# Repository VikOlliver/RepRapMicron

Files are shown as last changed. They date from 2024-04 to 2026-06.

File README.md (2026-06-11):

# RepRapMicron (μRepRap)

## Overview

The RepRapMicron Project, or μRepRap, is an extension of the Open Source RepRap 3D printer project that aims to bring micron-scale fabrication into very widespread adoption. The main project page is [here](https://reprap.org/wiki/RepRapMicron) and currently the assembly instructions are on the Github wiki. It uses hardware and software familiar to 3D printer and CNC developers (GCODE, GRBL, NEMA17 steppers etc.), and materials that are easily and inexpensively available.

As of PIKA V0.02 pixels can be placed or engraved with repeatable micron precision in 2D without difficulty. Range of motion is approximately 8mm on X, Y, and Z axes. A resin deposition system for <4μm droplets is functional if not complete. Current resin material is "Top Coat" Nail Art UV Gel.

The meaty part is in the "pika" directory, where the OpenSCAD models for a 3D printed print-in-place flexure chassis and axis drivers can be found. Parts are intended to fit a 10mm grid and attach with M3 fasteners.

The PIKA version is now the focus of development, and departs from MAUS in that it is specifically a μRepRap design, rather than a kit of parts for constructing μRepRaps. If you want to make the best practical machine rather than a flexure research platform, PIKA is the preferred version.

The project has achieved the fourth Alpha release. This repository holds files that can reasonably be expected to be functional and useful to potential developers/experimenters.

If you're looking for pre-built STL files for MAUS, they're [here](https://www.printables.com/model/1286343-reprapmicron-micron-accurate-3d-printer). PIKA is [here](https://www.printables.com/model/1692745-reprapmicron-pika-micron-resolution-3d-printer). Note that Printables is not automatically kept in sync with the source or instructions.

## Roadmap

1. Develop a micron-accurate, 3D printable mechanism. - UNLOCKED
2. Develop a print head for it. - UNLOCKED
3. Make more of them - UNLOCKED
4. Develop practical 3D deposition for resin and other materials.
5. Reduce further to nanoscale
6. Take over the world

## Directory Structure

### gcode_segmentation
Python code to take GCODE from a 3D printer slicing program such as PrusaSlicer, and break it into GCODE for a series of points that can be invidivually deposited with the probe. There is provision for a routine to "re-ink" the probe tip after a predetermined number of points are deposited.

### library
A Selection of useful OpenSCAD libraries used in generating "Metriccano" modular components (10mm grid, metric fasteners), screw holes, motor mounts etc.

### maus
**M**icron **A**ccurate **U**niversal **S**ystem - OpenSCAD model files for micron precision axis components based on flexures.

The maus directory contains standard axis drivers, XY complementary flexure Table, Z Tower, and probe parts that need screwing down to a solid surface. It can be assembled on a Metriccano baseboard supplied for lasercutting as metriccano_baseboad.svg, or a 12 x 14 hole piece of 10mm pitch perf board.

As of V0.05 a pantograph-like driver with parallelogram flexures - maus_parallelogram_axis_driver.scad - is used as the Axis Driver. This is linear in action rather than the earlier small-arc pivoting Axis Drivers, has a greater range of motion (~8mm TBD), and due to the linear motion of the drive nut has lower friction allowing higher acceleration and motion speed.

Assembly documentation for a functional release is on the Github Wiki, with configuration and usage instructions next up. Bill Of Materials available for V0.03 .

### pika
**P**rint **I**n-place **K**inematic **A**ssembly - OpenSCAD model files for a flexure-based axis system. The XY Table mechanism is print-in-place, making it more rigid and easier to assemble. Axis Drivers are similar to MAUS but have a modifed motor bracket component.

### png_to_gcode
Python code that reads a PNG bitmap and emits GCODE that will probe a corresponding point on the GCODE-controlled hardware. Pitch, brightness level and so forth can be provided on the command line. Intended for using RepRapMicron in dip-pen mode with bitmap files, but probably has other uses.

### oldGRBLdelta
A python/Zelle Control Panel that drives a GRBL CNC using xyz steppers and uses them to control an OpenFlexure microscope delta stage.

### utils
Utilities for calibration and assembly.

## Contributing
Please do join in. We need everything. Coders, makers, nanoscience experts, materials scientists, 3D printing experts, manual writers, graphics artists, dancers, the works. Well, maybe not the dancers.

The main repository of knowledge is the wiki on the [main project page](https://reprap.org/wiki/RepRapMicron). General updates go on [the blog](http://blog.reprap.org/). There is some coverage on the Facebook RepRap page, and commentary is welcomed.

## Licence
GPL V3 or later

## Project status
### PIKA V0.02

Fourth release candidate. Now the focus of development. Build process has been documented, other documentation relies on its compatibility with MAUS.

### MAUS V0.05

Third Alpha release candidate designed for flexure research. Essentially a modification to use PIKA-style linear Axis Drivers.

### MAUS V0.04

The prefereble build if documentation is required. V0.04 documentation is currently a list of fixups for V0.03 docs.

### MAUS V0.03

First ever Alpha release. Tested build with a few known flaws and full build documentation on wiki.

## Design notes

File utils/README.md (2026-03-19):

# RepRapMicron (μRepRap) Utilities

## Overview

This directory contains a number of utilites for aligning and calibrating the μRepRap axes.

## backlash_vernier.py

Creates a GCODE file for determining backlash on either the X (default) or Y axis. Use --help for details. Intended to be used with a probe engraving a marker substrate.

The default settings draw two sets of lines, one drawn away from the origin at a spacing increasing by 0.5μm each time, the other drawn towards the origin at constant spacing.

By observing the point at which the lines appear to align, the amount of backlash can be determined. Remember that backlash is occurring in both sets of lines in opposite directions.

## grid_gcode.py

Creates GCODE to draw a grid, default settings 10 x 10 squares of 100μm. THe grid is created using full-length lines across the grid rather than by drawing each square individually.
Useful for determining overall behaviour of the axes when engraving with the probe on a marker substrate.

## levelling_probe.py

Directly drives GCODE-based CNC through a USB serial port. μRepRap is fitted with a Touch Plate - a conductive flat slide connected to one side of the Z Touch CNC input.

This console-based utility does a simple probe on an area (by default 1mm on each side) and indicates the highest corner, lowest corner, and the overall height variation.

Given the accuracy of a foil-covered slide, a height variation of under 4μm is considered reasonable.

It is advisable to run this utility serveral times before relying on any given values because the probe physically interacts with the surface and it may take a few passes for things to stabliize.

The wider the area covered, the more accurate overall levelling will be.

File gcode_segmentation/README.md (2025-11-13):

# RepRapMicron (μRepRap) "Dipify" GCODE Segmentation

## Overview

These are the files used by The RepRapMicron Project, or μRepRap, to create GCODE from an STL or SVG file using PrusaSlicer that will draw the lines with individual dots of resin. Currently only works with one layer.

It is designed to emit GCODE on a scale of 1mm to 1 micron in the PrusaSlicer config, hopefully the same as you have configured your GRBL or other CNC controller to. Because PrusaSlicer cannot cope with print widths and layer heights on this scale, a scaling factor (set to 10 by default) lets you work on a scale of 1mm to 10 microns. Note that the scaling factor applies to both distance and speed.

## How it works

When you export the sliced model, the prusa_filter.sh bash script takes Prusa's GCODE filename as the first parameter. It is basically there to handle temporary files and call some python. I found it useful for debugging so I left it there.

The dipify_gcode.py looks for the first "Layer" comment in the GCODE and uses that to determine the layer height. It then scans the GCODE to find lines drawn below the safe Z height and breaks those line into segments. The probe is lowered to the current layer height to touch the print bed and leave a resin dot. These segments are smaller than the resin dot RepRapMicron deposits, so a line of joined dots will be created.

Some GCODE such as A axis movement and M commands are discarded.

After a given number of dots are deposited, the probe is taken to the reservoir coordinates and dipped in resin. A UV LED on the coolant output of the CNC controller is briefly turned on while the probe is in the resin reservoir (note: this is protected from the UV). Then it returns to the last point and continues.

The points are sanity checked for proximity, so for things like arcs constructed of many short lines, points are not deposited on top of one another.

At the start of each layer other than the first, the probe is dunked in the resin and the UV LED is turned on to solidify the layer.

At the end of the GCODE the script expects to find a "; *END" comment, at which point it will safely move the probe into the reservoir and do a final and longer UV exposure.

## Notable WeirdnessCompared To Conventional Extruders

FFF extruders squirt plastic down from a known height. The RepRapMicron deposits resin at the layer height, with the resin buildup above the probe tip. To work around the slicer implications, print the first layer with a negligible layer height.

FFF Extruders will drop their exudate down towards the bed, and if the layer height is set a bit tall a loosely consolidated print will result. If the RepRapMicron probe does not reach a previous layer when attempting a second layer it will not deposit any resin there or on subsequent layers and you get no output at all.

## Setting up

Load a new slide into the RepRapMicron, add a thin smear (not a drop) of resin on the foil contact plate right up to the folded over edge of the plate. Do not get resin on the folded part. That is the barrier between the resin and the build area.

Position the probe over the glass slide nearby.

Using your CNC control software move over the resin and do a "Z Touch" with the probe.

Raise the probe 100 microns or so and move it to an area of glass where you will not be depositing resin. Lower the probe to about 5 microns over the glass, or until it just deposits a droplet of resin in the slide (you'll have to move the probe up and sideways to spot it).

Set this as the Z zero and raise the probe to 100 microns or so again. Move the probe above the resin, lower it until it is in the resin. This is your reservor Z value, typically around 25μm and once determined seldom needs adjustment. Reservoir X and Y are variables in the script, but it is very convenient to arrange things so that the reservoir is at X=0, Y=-1000.

Do not get the probe too close to the reservoir edge or the UV light will solidify resin on the probe.

Load the GCODE into your CNC control software and run, finger poised over the HALT switch in a distrustful manner.

Fine tuning segment sizes and number of points per dip is left as an exercise to the diligent student.

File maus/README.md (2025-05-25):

# **M**icron **A**ccurate **U**niversal **S**ystem- “Maus”

## Overview
Maus is a collection of micron-accurate components based on 3D printed flexures. These can be combined into a multi-axis motion stage allowing a probe (or probes) to be manipulated.

The probe can be manoeuvred around a standard 25mm x 75mm glass microscope slide. Micron-level movement in the default configuration is expected to be possible inside a 4mm cube, and non-destructive movement (basically to get the probe out of the way) inside an 8mm cube. The probe can be used as a dip pen for depositing UV resin and other liquids from a reservoir on the slide. The probe is conductive and can be used to scan conductive objects via a ground wire on the slide holder.

A window in the stage allows UV exposure of the resin from underneath without illuminating the reservoir. Motion is achieved with a 400 step NEMA17 stepper motor on each axis driver, and these are controlled by any method convenient for the user.

The intention is that the probe will also be used to manipulate or even operate micron-scale items.

## Build
The *maus* directory contains three main Maus OpenSCAD build files, a design for a probe box, and the deprecated XY Table design:

**maus_axis_driver.scad** has the flexure-based precision axis driver design that is driven by a NEMA17 stepper motor.

**maus_complementary.scad** is the XY Table and stage design using complementary flexures. These have the great advantage that they do not move much in the Z axis when moving in the X & Y axes. Also contains clamp design for cylindrical USB miscroscopes.

**flexure_linear_coupling.scad** is a model for a couping that press fits on a NEMA17 motor shaft, and given sufficient downward pressure can hold a modified M3x50 screw. The screw has the head filed down in a drill so that it is narrower in diameter than the narrowest axis of an M3 nut, and the nut is screwed all the way down to the head, where it is secured with Loktite. The tapered hexagonal hole in the top of the coupling holds on to the nut.

**probe_electrolysis_grip.scad** provides a convenient jig for making micron probe tips from 28ga stainless steel or nichrome wire. 5% salt solution is used as the electrolyte, and the extremely simple process is described at [https://www.printables.com/model/874566](https://www.printables.com/model/874566).

## Deprecated

**maus_stage_deprecated.scad** Original XY Table design, now deprecated. Has at its bottom three *if (true/false)* statements used to print a selected set of parts for either an axis driver (you probably want three of those), a slide probe assembly, or an XY Table. It uses SCAD files included from the ../include directory.

**metriccano_flexures.scad** Deprecated. Has the 2-way flexure joints used for an XY Table in it, and is included by maus_stage_deprecated.scad . This should probably be in the include directory, but there are too many dependencies, I haven't figured out a nice way yet, and deprecated anyway.

## Recommended Software
To control the stepper motors, an Arduino running GRBL and a 3-axis GRBL stepper shield are adequate. GCODE can be conveniently output by 3D printer or CNC programs, though it is recommended that a scale of 1mm to 1 micron is used to avoid floating point errors. The author uses an Arduino Mega running GRBL and driving a RAMPS1.4 3D printer control board. To generate the GCODE they use Inkscape to create SVG files, convert those to GCODE with jscut, and use cncjs as a control console. There are also a number of Python scripts in the repository for converting a PNG file to GCODE coordinates, and to act as a processing filter to allow PrusaSlicer to create μRepRap GCODE.

## Documentation
There is some in the Github Wiki, though I've been busy making it work and haven't written it all yet. Experiences are logged on the RepRap Blog http://blog.reprap.org (yes, that is http, the project is rather old).

Hopefully there will be some videos made, as we've just had a videographer volunteer. But Everything Open conference presentation is near, and planning has to be done etc.

## Todo
The next big thing is to get the UV LED curing a layer automatically, and then building a second layer on top of it.

A callibration test part for determining the flexibility of flexures printed in specific plastics has been designed, but it has not been quantitatively described.

## Printing
The parts are designed to be printed from quality PLA with no support. A brim is only likely to be needed on the Flexible Linear Coupling. Some printers may have difficulty printing the long beams, in which case use a brim for only those parts. The design expects 0.2mm layers with perimeters and wall thicknesses optimised for strength. As a starting point, use 4 walls and 20% infill. The author uses a Prusa Mk4 with a 0.4mm nozzle loaded with either eSun PLA+ filament or Diamond Age/Imagin Ingeo PLA. Recommendation is to not use ASA, PETG, exotic filaments, matt finish, metallic-filled and so forth as these tend to be stiffer and cause the structure to flex undesirably. The height (and thus flexibility) of the flexures can be tuned in the *maus_*.scad* files if specific filaments or materials are required.

## Pre-built STL Files
If you just want to print bits and play with them, the 0.02 version can be found on Printables at [https://www.printables.com/model/1124932](https://www.printables.com/model/1124932) though these are not guaranteed to be up-to-date, and may not work if your filament is particularly flexible or rigid. The V0.03 STL files built by current code are still being tested, but should be released relatively soon.

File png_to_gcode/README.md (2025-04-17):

# png_to_gcode Utility

# Overview
This takes a PNG image and parses it pixel by pixel. It creates GCODE that moves a CNC tool head (or μRepRap probe) to probe either dark or light pixels.

It takes and outputs either from files or STDIO, and light/dark/movement/height etc. are all configurable from the command line.

use png_to_gcode -h for detailed help.

## Improvements
This needs code to optionally implement a "dip pen" function like gcode_segmentation where the probe is dipped in a resin reservoir after however many points are plotted. In fact, multiple reservoirs might be useful, allowing pixels in various colours to be plotted using different resins (obvious complexities like cleaning the probe tip are left as an excercise to the individual). Perhaps this should be in a shared library?

## Rationale
The idea for this emerged because of the gcode_segmentation 3D printer filter. Why, I thought, go to all the trouble of making vectors and turning them into pixels when you can just create a pixel map? It has a drawing height programmable from the command line, so in theory could do multiple layers. At the very least people are goign to print bitmap logos with it.

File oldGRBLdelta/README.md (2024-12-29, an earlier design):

# μRepRap GRBL Delta Controller

## Overview
This code was written in the early stages of development to allow a GRBL XYZ controller to be driven in a such a way that it could control a Delta configuration axis. At present it is not under development, but in the way of things it could be resurrected later or cannibalised.

## Files
The main python file is deltacontrol.py which uses the Zelle portable python graphics library. Just copy graphics.py into the same directory along with the other .py files.

The Control Panel drives a GRBL CNC using xyz steppers and uses them to control an OpenFlexure microscope delta stage. I've modified my GRBL config to home x, y and z simultaneously. The GRBL setup I've used is included. I used [GRBL-Servo](https://github.com/robottini/grbl-servo) and a RAMPS board as my controller, but it should work with other GRBL controllers

## Assembly

3D model files modified or generated for μRepRap are here:
https://www.printables.com/model/827788-probe-arm-and-endstop-switch-feet-for-openflexure
https://www.printables.com/model/797699-openflexure-delta-microscope-mods-to-fit-nema17-st

You will need the delta stage file delta_stage_multipath_microscope_reinforced.stl to fit the probe parts to.

Other parts and assembly details for the stage are found on the [OpenFlexure site](https://build.openflexure.org/openflexure-delta-stage/v1.2.2/pages/index_reflection.html). Only the stage assembly itself is required but you will at least need their 'O'-ring insertion tool. The fancy base and Raspberry Pi components are not needed.

## Contributing
Please do join in. We need everything. Coders, makers, nanoscience experts, materials scientists, 3D printing experts, manual writers, graphics artists, dancers, the works. Well, maybe not the dancers.

The main repository of knowledge is the wiki on the main project page. General updates go on [the blog](http://blog.reprap.org/). There is some coverage on the Facebook RepRap page.

## License
Everything possible is under the GPL.

## Project status
Pre-pre-alpha.

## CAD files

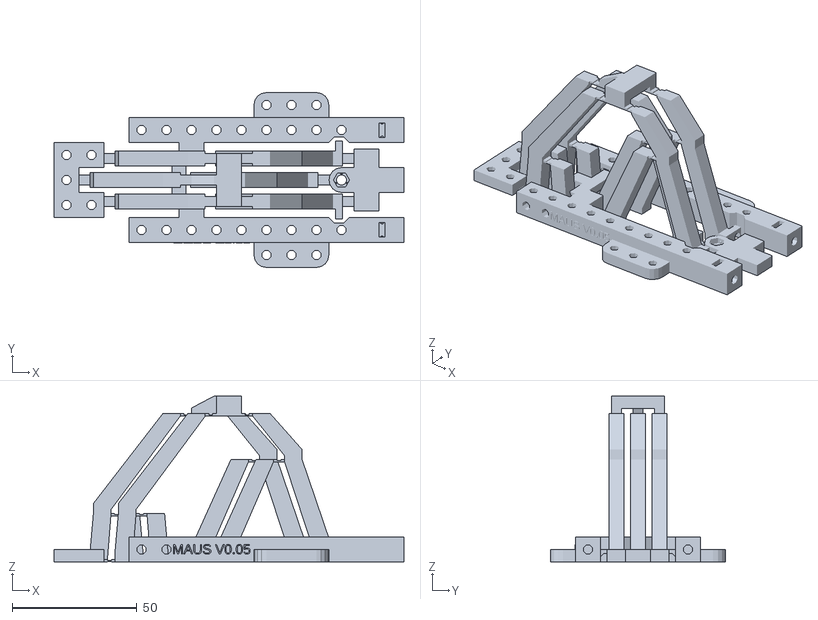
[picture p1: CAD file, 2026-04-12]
pika/frame_trio.stl
140.1 x 70.0 x 66.3

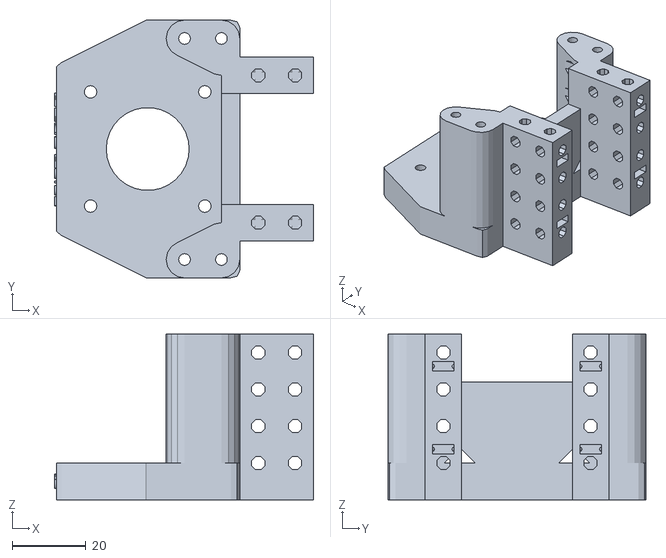
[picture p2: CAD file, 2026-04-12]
pika/motor_pillar_pika.stl
70.3 x 70.0 x 45.0

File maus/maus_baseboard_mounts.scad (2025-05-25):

// maus_baseboard_mounts.scad - Mounting parts for optional double-layer baseboard
// (c)2025 vik@diamondage.co.nz, released under the terms of the GPL V3 or later

version_string="MAUS V0.03";

include <../library/m3_parts.scad>
include <../library/metriccano.scad>


// 0.6mm thick text, 5mm tall, vertical, flat on XY plane
module version_text() {
    translate([0,0,-0.3]) linear_extrude(0.6) {
        text(version_string, size = 4, halign = "center", valign = "center", $fn = 16);
    }
}

// 50mm pillars in L-shape with nut cavities
module baseboard_pillar() {
    translate([0,0,metriccano_unit]) rotate([180,0,0]) metriccano_square_strip(5);
    translate([0,0,metriccano_unit]) metriccano_square_strip(5);
    translate([0,metriccano_unit,0]) metriccano_square_strip(5);
}

// Foot with screw head recesses
module baseboard_foot() difference() {
    // Nice tapered plate
    hull() {
        metriccano_plate(2,2);
        translate([0,0,metriccano_unit/2]) scale([1.1,1.1,1]) metriccano_plate(2,2);
    }
    // Bunch of screw holes
    translate([0,0,metriccano_unit/2]) metriccano_screw_cavity(20);
    translate([metriccano_unit,0,metriccano_unit/2]) metriccano_screw_cavity(20);
    translate([0,metriccano_unit,metriccano_unit/2]) metriccano_screw_cavity(20);
    translate([metriccano_unit,metriccano_unit,metriccano_unit/2]) metriccano_screw_cavity(20);
}

baseboard_pillar();
translate([60,0,0]) baseboard_foot();

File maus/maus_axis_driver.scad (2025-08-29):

// maus_axis_driver.scad - RepRapMicron motion stage
// (c)2024 vik@diamondage.co.nz, released under the terms of the GPL V3 or later
// One Maus Axis Diver. Three are needed for the complete Maus mechanism
//
// V0.04 Updates:
// Lowering the wall on the Axis Motor Pillar Assembly to allow larger range of movement
// added mounting holes for extra rigidity
// Through holes on NEMA plate to allow pillar screw overtravel

version_string="MAUS V0.04";

include <../library/m3_parts.scad>
include <../library/nema17lib.scad>
include <../library/metriccano.scad>

flexure_width=6;        // Reduced from original 7.
flexure_length=2.5;
flexure_height=1.0;     // For DIAS PLA, 1 is about right. Testing 0.8 for stiffer filament
vertical_flexure_length=8;
vertical_flexure_height=6;
vertical_flexure_width=8;   // Width of the anchor block
vertical_flexure_thick=8.2; // Width of the actual flexing bit

// Used to fiddle flexures. Just over one layer...
layer_height=0.21;
wall=2;                         // Arbitrary rigid wall thickness

// These define the size and mechanical advantage of the whole mechanism. Overall dimensions change to suit.
/*axis_arm_ratio=2.5;
axis_lifter_length=25;
axis_arm_length=axis_lifter_length*axis_arm_ratio;*/
axis_lifter_length=24;
axis_arm_length=72;
axis_arm_ratio=axis_arm_length/axis_lifter_length;
echo(str("Arm ratio=",axis_arm_ratio));

axis_probe_depression=2;       // Shouldn't this be 4 not 2?

/* Valuse used for the original Z axis
axis_arm_ratio=4;
axis_lifter_length=14;
axis_probe_depression=2;
*/


axis_motion_clearance=axis_probe_depression+0.5;    // This should clear moving parts...
axis_arm_width=12;
axis_lifter_width=flexure_width;
axis_lifter_height=4;
axis_platform_height=40;   // Height of the Z platform with mounting holes in.
axis_platform_thick=3;        // Thickness of Z platform with holes in.
platform_pivot_width=30;    // Maximum horizontal separation of flexures (edge to edge) on platform
platform_surface_width=40;  // Horizontal dimension of platform surface (Y axis)

// The fixed block on which the platform pivots
axis_anchor_block_length=platform_pivot_width;
axis_anchor_block_width=8;
axis_anchor_block_height=7;
axis_arm_height=axis_anchor_block_height+axis_motion_clearance;
axis_drive_pivot_x=axis_arm_length-axis_arm_length/axis_arm_ratio;  // Z drive flexure on X
axis_nut_holder_rad=6;                 // Diameter of the thing that holds the drive nut
axis_drive_nut_x=axis_drive_pivot_x+flexure_length/2+axis_nut_holder_rad;           // Z drive nut on X
drive_lug_length=18;                    // Length of the transverse drive lug bar.
axis_top_bearing_z=29;             // Bottom of the bearing block is this far off the base

// Where the flat, long arm starts near the anchor
axis_end_bend_x=axis_anchor_block_width+flexure_length/2+axis_motion_clearance;

// Function to calculate the distance between two points
function distance(x1,y1,x2,y2) = sqrt(pow(x1-x2, 2) + pow(y1-y2, 2));

// 0.6mm thick text, 5mm tall, vertical, flat on XY plane
module version_text() {
    translate([0,0,-0.3]) linear_extrude(0.6) {
        text(version_string, size = 4, halign = "center", valign = "center", $fn = 16);
    }
}

// Selection of holes that line up with the pillars supporting
// the complete axis over the motor
module pillar_screw_holes() {
    translate([metriccano_unit,-3*metriccano_unit,-0.001]) {
        cylinder(h=axis_motor_pillar_height*3,r=metriccano_screw_rad,$fn=16,center=true);
        metriccano_nut_cavity_tapered(captive=true) ;
    }
    translate([metriccano_unit,3*metriccano_unit,-0.001]) {
        cylinder(h=axis_motor_pillar_height*3,r=metriccano_screw_rad,$fn=16,center=true);
        metriccano_nut_cavity_tapered(captive=true) ;
    }
    translate([2*metriccano_unit,3*metriccano_unit,-0.001]) {
        cylinder(h=axis_motor_pillar_height*3,r=metriccano_screw_rad,$fn=16,center=true);
        metriccano_nut_cavity_tapered(captive=true) ;
    }
    translate([2*metriccano_unit,-3*metriccano_unit,-0.001]) {
        cylinder(h=axis_motor_pillar_height*3,r=metriccano_screw_rad,$fn=16,center=true);
        metriccano_nut_cavity_tapered(captive=true) ;
    }
}


// Mounting plate for a NEMA17 motor with rounded corners,
// Extended width for metriccano mounting
// nema_late_thick - Thickness of NEMA mounting plate
// nema_corner_rad - radius of rounded corners
module nema17_plate(nema_plate_thick=5,nema_corner_rad=2) difference() {
    rad_loc=(5*metriccano_unit-nema_corner_rad)/2-1;
    hull() {
        // +Y side
        translate([rad_loc,rad_loc+metriccano_unit,0]) cylinder(h=nema_plate_thick,r=nema_corner_rad);
        translate([-rad_loc,rad_loc/2+metriccano_unit,0]) cylinder(h=nema_plate_thick,r=nema_corner_rad);
        // _Y side
        translate([rad_loc,-rad_loc-metriccano_unit,0]) cylinder(h=nema_plate_thick,r=nema_corner_rad);
        translate([-rad_loc,-rad_loc/2-metriccano_unit,0]) cylinder(h=nema_plate_thick,r=nema_corner_rad);
        // Central markers where we start narrowing the end down
        translate([0,-rad_loc-metriccano_unit,0])
            cylinder(h=nema_plate_thick,r=nema_corner_rad);
        translate([0,rad_loc+metriccano_unit,0])
            cylinder(h=nema_plate_thick,r=nema_corner_rad);

    }
    // Screw holes
    translate([nema17_screw_sep/2,nema17_screw_sep/2,0]) cylinder(h=nema_plate_thick*3,r=m3_screw_rad,$fn=16,center=true);
    translate([-nema17_screw_sep/2,nema17_screw_sep/2,0]) cylinder(h=nema_plate_thick*3,r=m3_screw_rad,$fn=16,center=true);
    translate([nema17_screw_sep/2,-nema17_screw_sep/2,0]) cylinder(h=nema_plate_thick*3,r=m3_screw_rad,$fn=16,center=true);
    translate([-nema17_screw_sep/2,-nema17_screw_sep/2,0]) cylinder(h=nema_plate_thick*3,r=m3_screw_rad,$fn=16,center=true);
     // Collar hole
    cylinder(h=nema_plate_thick*3,r=nema17_collar_rad,center=true);
    // Relief holes for over-travel of pillar screws
    pillar_screw_holes();
}

// A NEMA17 plate with nutted Metriccano mounting holes, pillars to prop up the axis flexure mechanism,
// and hold a limit switch.
// Why does it have a separate base plate? Because M3 screws come in standard lengths and it needs a spacer.
axis_motor_pillar_height=34;
limit_switch_level=28.0;    // Height to the top of the limit switch bar
motor_pillar_spacing=6*metriccano_unit;     // Pillar holes, centre to centre
motor_base_thick=10;
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

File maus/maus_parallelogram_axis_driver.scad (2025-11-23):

// maus_axis_driver.scad - RepRapMicron motion stage
// (c)2025 vik@diamondage.co.nz, released under the terms of the GPL V3 or later
// Prototype Linear Maus Axis Diver
// Uses a pantograph-like mechanism, paralleled up to provide stable
// drive, anchor, and effector ends.
//
// Note: It is a Very Good Idea(TM) to keep all the mounting and fixing points
// close to 10mm centres. If necessary, tweak angles, ratios, and arm lengths to do this.

version_string="MAUS V0.05";

include <../library/m3_parts.scad>
include <../library/nema17lib.scad>
include <../library/metriccano.scad>

flexure_width=4;
flexure_length=2.5;
flexure_height=1.0;     // Thickness of the flexure block including footings
flexure_thickness=0.6;  // Thickness of the actual flexure part
flexure_tab_length=flexure_length+2;    // Distance between two attachment zones.
vertical_flexure_length=8;
vertical_flexure_height=6;
vertical_flexure_width=8;   // Width of the anchor block
vertical_flexure_thick=8.2; // Width of the actual flexing bit

// Used to fiddle flexures. Just over one layer...
layer_height=0.21;
wall=2;                         // Arbitrary rigid wall thickness

reduction_ratio=0.685;    //  Amount we want to reduce the movement by

arm_angle=55.2;   // Angle of the paralellogram. Zero is flat.

// Length of a parallelogram main arm
pll_main_arm_length=71;
//pll_main_arm_at_45=sqrt(pll_main_arm_length*pll_main_arm_length/2);
pll_main_arm_x=pll_main_arm_length*cos(arm_angle);
pll_main_arm_y=pll_main_arm_length*sin(arm_angle);
pll_main_arm_at_45=pll_main_arm_x;

pll_beam_end_flat_height=flexure_height+1.5;
pll_beam_x=7;  // Parallelogram beam width along the X axis
pll_beam_y=flexure_width+2;
pll_platform_beam_length=metriccano_unit;
// Bottom beam is higher than top beam as it has to fit between moving flexures
pll_top_beam_height=3;
pll_bottom_beam_height=10;
// Distance between the two most distant flexures
pll_flexure_to_flexure=pll_main_arm_x*2+flexure_tab_length+pll_platform_beam_length;

echo("End fixing separation =",pll_flexure_to_flexure+flexure_tab_length+metriccano_unit);

pll_arm_a_length=pll_main_arm_length*(1-reduction_ratio);
pll_arm_a_x=pll_arm_a_length*cos(arm_angle);
pll_arm_a_y=pll_arm_a_length*sin(arm_angle);
pll_arm_b_length=pll_main_arm_length*reduction_ratio;
pll_arm_b_x=pll_arm_b_length*cos(arm_angle);
pll_arm_b_y=pll_arm_b_length*sin(arm_angle);


// Distance from frame center to frame center (leave gap so they dont rub).
pll_frame_centres=metriccano_nut_max_width+2;
// Calculate the gap between frames
pll_frame_spacing=pll_frame_centres-pll_beam_y;

side_beam_length=metriccano_unit*11;
side_beam_width=metriccano_unit;
side_beam_height=metriccano_unit;
side_band_indent=2.5;      // Indent sides by this much to allow band hooks to pass
 
// A flexure joint for printing it on the surface of the print bed. Footings extend 1mm.
// "flat" will print without an undercut
module flexure_tab(flat=false) difference() {
    translate([0,0,flexure_height/2]) cube([flexure_tab_length+2,flexure_width,flexure_height],center=true);
    if (flat) {
        // Hollow just the top of the flexure
        translate([0,0,flexure_height]) 
            cube([flexure_length*0.6,flexure_width*3,flexure_thickness*2],center=true);    
    } else {
        // Hollow the top of the flexure
        translate([0,0,flexure_height+layer_height]) 
            cube([flexure_length*0.6,flexure_width*3,flexure_thickness*2],center=true);    
        // Undercut the flexure so it does not touch print bed
        cube([flexure_length*0.6,flexure_width*3,layer_height*2],center=true);
    }
}

// A flexure join that will be printed suspended in air
module flexure_tab_unsupported() difference() {
    translate([0,0,flexure_height/2]) cube([flexure_tab_length+1,flexure_width,flexure_height],center=true);
    // Scalop the top of the flexure
    translate([0,0,flexure_height]) cube([flexure_length*0.6,flexure_width*3,flexure_height],center=true);
}

// Flat end of a beam, levelled on Z=0, centred on X=Y=0
// Made smaller for the top layer
module pll_beam_end(l=pll_beam_end_flat_height) {
    translate([-pll_beam_x/2,-pll_beam_y/2,0])
        cube([pll_beam_x,pll_beam_y,l]);
}

module pll_long_arm() {
    pll_beam_end();
    hull() {
        translate([0,0,pll_beam_end_flat_height]) pll_beam_end();
    translate([pll_main_arm_x,0,pll_main_arm_y]) pll_beam_end();
    }
}

module pll_arm_a() {
    pll_beam_end();
    hull() {
        translate([0,0,pll_beam_end_flat_height]) pll_beam_end();
    translate([pll_arm_a_x,0,pll_arm_a_y]) pll_beam_end();
    }
}

// Create an arm with a flexure on each end between (0,0) and (x,y).
// Reverse will make the flexures point in opposite directions.
// We may need to extend the base of the arm away from the Drive Screw
// or the arm will collide with the upper_nut_bar then it is driven down.
module pll_flexure_arm(x,y,reverse=false,extend_base=0)  {    
    // First flexure, placed on 0,0
    flexure_tab();
    if (reverse) hull() {
        // Join up the extension so that it is alwaus a solid baem.
        translate([(extend_base+pll_beam_x+flexure_tab_length)/2,0,0]) pll_beam_end();
        translate([(pll_beam_x+flexure_tab_length)/2,0,0]) pll_beam_end(metriccano_unit/2);
    }
    else
        translate([(-pll_beam_x-flexure_tab_length)/2,0,0]) pll_beam_end();
    // The beam bit
    hull() {
        if (reverse) {
            translate([(extend_base+pll_beam_x+flexure_tab_length)/2,0,pll_beam_end_flat_height]) pll_beam_end();
            translate([x+(-pll_beam_x-flexure_tab_length)/2,0,y]) pll_beam_end(flexure_height);
        } else {
            translate([(-pll_beam_x-flexure_tab_length)/2,0,pll_beam_end_flat_height]) pll_beam_end();
            translate([x+(-pll_beam_x-flexure_tab_length)/2,0,y]) pll_beam_end(flexure_height);
        }
    }
    // Second flexure  placed on the mark
  
  translate([x,0,y]) flexure_tab(flat=true);
}

// Main arm wiht a kink where the centre flexure goes
module bent_pll_arm(ratio,extend_base=0) {
    pll_flexure_arm(pll_main_arm_x*(1-ratio),pll_main_arm_y*(1-ratio),true,extend_base);
    translate([pll_main_arm_x*(1-ratio),0,pll_main_arm_y*(1-ratio)])
        pll_flexure_arm(pll_main_arm_x*ratio,pll_main_arm_y*ratio);
}

// Pantograph arm with platforms in the middle and at each end
module centre_pll_arm() {
    // The -X arm
    bent_pll_arm(reduction_ratio) ;
    // The +X arm, with Arm B and beam platform on it.
    translate([pll_main_arm_x*2+pll_platform_beam_length+flexure_tab_length,0,0])
        rotate([0,0,180]) {
            // Main arm. Extend the base out to avoid collision with upper_nut_bar
            bent_pll_arm(1-reduction_ratio,extend_base=8);
            // Arm B
            translate([pll_arm_b_x*2,0,0]) rotate([0,0,180])
                pll_flexure_arm(pll_arm_b_x,pll_arm_b_y,true);
            translate([pll_arm_b_x*2+(flexure_tab_length+pll_platform_beam_length)/2,0,pll_bottom_beam_height/2])
                cube([pll_platform_beam_length,pll_beam_y,pll_bottom_beam_height],center=true);
    }
            
    // Arm A
    translate([pll_arm_a_x*2,0,0]) rotate([0,0,180])
        pll_flexure_arm(pll_arm_a_x,pll_arm_a_y,true);
        
    // The top beam. Make sure it rests on top of the flexure...
    translate([pll_main_arm_x+pll_platform_beam_length/2+flexure_tab_length/2,0,pll_main_arm_y+pll_top_beam_height/2]) 
        cube([pll_platform_beam_length,flexure_width,pll_top_beam_height],center=true);
}

// Tags to connect to flexures Heads off in -X, -Y and right end is at X=0.
module fixed_arm_flexure_tag() {
    // This bit goes on the flexure
    hull() {
        translate([1,(metriccano_unit-flexure_width*1.5)/2,flexure_height/2])
            cube([1,flexure_width,flexure_height],center=true);
        // This bit hides inside the metriccano strip
        translate([0.2-pll_platform_beam_length+flexure_tab_length/2+metriccano_screw_rad,0,metriccano_unit/4])
            cube([0.1,metriccano_unit/2,metriccano_unit/2],center=true);
    }
}
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

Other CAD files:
maus/probe_electrolysis_grip.scad
UV_head/UV_Module_to_fibre.scad
UV_head/optic_probe_holder.scad
maus/flexure_linear_coupling.scad
maus/maus_complementary.scad
maus/maus_pika.scad
maus/maus_probe.scad
maus/maus_stage.scad
maus/maus_stage_deprecated.scad
maus/maus_z_tower.scad
maus/metriccano_flexures.scad
maus/probebox.scad
pika/microscope_clamps.scad
pika/pika_axis_driver.scad
pika/pika_probe.scad
pika/pika_touch_probe.scad
pika/pika_version.scad
pika/pika_xy.scad

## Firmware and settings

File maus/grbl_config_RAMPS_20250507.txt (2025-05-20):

$0=10 (Step pulse time, microseconds)
$1=255 (Step idle delay, milliseconds)
$2=0 (Step pulse invert, mask)
$3=4 (Step direction invert, mask)
$4=0 (Invert step enable pin, boolean)
$5=0 (Invert limit pins, boolean)
$6=0 (Invert probe pin, boolean)
$10=17 (Status report options, mask)
$11=0.100 (Junction deviation, millimeters)
$12=0.200 (Arc tolerance, millimeters)
$13=0 (Report in inches, boolean)
$20=0 (Soft limits enable, boolean)
$21=1 (Hard limits enable, boolean)
$22=1 (Homing cycle enable, boolean)
$23=3 (Homing direction invert, mask)
$24=5000.000 (Homing locate feed rate, mm/min)
$25=5000.000 (Homing search seek rate, mm/min)
$26=10 (Homing switch debounce delay, milliseconds)
$27=1800.000 (Homing switch pull-off distance, millimeters)
$30=1000 (Maximum spindle speed, RPM)
$31=0 (Minimum spindle speed, RPM)
$32=0 (Laser-mode enable, boolean)
$100=33.830 (X-axis travel resolution, step/mm)
$101=33.642 (Y-axis travel resolution, step/mm)
$102=44.444 (Z-axis travel resolution, step/mm)
$110=6000.000 (X-axis maximum rate, mm/min)
$111=6000.000 (Y-axis maximum rate, mm/min)
$112=20000.000 (Z-axis maximum rate, mm/min)
$120=50.000 (X-axis acceleration, mm/sec^2)
$121=50.000 (Y-axis acceleration, mm/sec^2)
$122=900.000 (Z-axis acceleration, mm/sec^2)
$130=5500.000 (X-axis maximum travel, millimeters)
$131=5500.000 (Y-axis maximum travel, millimeters)
$132=5500.000 (Z-axis maximum travel, millimeters)

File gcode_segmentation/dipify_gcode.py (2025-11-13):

#!/usr/bin/env python3
# dipify_gcode.py - Revision 0.04
#
# A tool to process GCODE, subdividing toolpaths below a safe Z height into smaller segments.
# It moves the tool to safe Z height, touches down to original Z, and returns to safe Z
# for each segment. After a configurable number of points, it simulates a dip probe operation.
# This accepts GCODE made on a scale of 1mm = 10 microns and converts to 1mm = 1 micron
#
# Copyright (C) 2025 Vik Olliver
#
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
# TODO
#


import argparse
import sys
import math

# Configuration parameters
SAFE_Z = 30.0   # Safe Z height over layers when moving around with the probe
DIP_SAFE_Z = 200.0   # Safe Z height when dipping (must clear dip reservoir edge)
FAST_Z = 14000  # Fastest speed we want to move Z axis
SEGMENT_LENGTH = 8  # Length of segments (def 8)
PROBE_POINT_LIMIT = 30  # Number of points before calling dip_probe(). Set to zero for no dip (def 15)
# Location of the dipping reservoir
RESERVOIR_X = 0
RESERVOIR_Y = -1000
RESERVOIR_Z= 18
SCALE_FACTOR=10
SKIM_HEIGHT = 10  # We move this much above the deposition height between dots to stop the tip dragging
uv_enabled = True # Usually you will want this enabled, but I put this here for testing.

UV_EXPOSURE_LONG = 5;
UV_EXPOSURE_SHORT = 80;

# NOTE: Not implemented yet.
def parse_arguments():
    parser = argparse.ArgumentParser(
        description="Convert PrusaSlicer GCODE into GCODE dots for plotting or engraving.",
        formatter_class=argparse.ArgumentDefaultsHelpFormatter
    )
    parser.add_argument("input", help="Input PNG file (use '-' to read from stdin)")
    parser.add_argument("-o", "--output", help="Output GCODE file (use '-' for stdout)", default="-")
    parser.add_argument("-d", "--distance", help="Distance per pixel in CNC units", type=float, default=30.0)
    parser.add_argument("--safe-z", help="Safe travel height in mm", type=float, default=50.0)
    parser.add_argument("--draw-z", help="Drawing/contact height in mm", type=float, default=0.0)
    parser.add_argument("--dipify", help="Dip probe after this many pixels (>=0)", type=int, default=-1)   

    return parser.parse_args()


def probe_into_reservoir(current_position,output_stream):
    """
    Just poke the probe into the reservoir.
    """
    # Move the probe to the reservoir.
    output_stream.write(f"G1 Z{max(DIP_SAFE_Z,current_position[2]+SAFE_Z):.3f} F{FAST_Z:.3f} ; Moving to dip-safe Z\n")
    output_stream.write(f"G0 X{RESERVOIR_X:.3f} Y{RESERVOIR_Y:.3f} ; Moving to reservoir\n")         
    output_stream.write(f"G1 Z{RESERVOIR_Z:.3f} F{FAST_Z:.3f} ; Dip the probe\n")

def probe_out_of_reservoir_and_return(current_position,output_stream):
    """
    Lift the probe back out of the reservoir to a safe height, then send it back to current print position
    """
    output_stream.write(f"G1 Z{max(DIP_SAFE_Z,current_position[2]+SAFE_Z):.3f} F{FAST_Z:.3f} ; Moving to dip-safe Z\n")
    output_stream.write(f"G0 X{current_position[0]:.3f} Y{current_position[1]:.3f} ; Return probe\n")
    # Note: The caller will sort the Z height out

def dip_probe(current_position,output_stream):
    """
    Move the probe to the reservoir and dip the tip. Restore XY probe position after dip BUT NOT Z.
    """
    probe_into_reservoir(current_position,output_stream)
    # May as well give a quick UV blast while we're there
    expose_to_uv(output_stream,UV_EXPOSURE_SHORT);
    probe_out_of_reservoir_and_return(current_position,output_stream)
        # Note: The caller will sort the Z height out

def expose_to_uv(output_stream,exposure_factor):
    """
    While slowly raising the probe 10 microns, leave the UV LED on. This gives us
    the LED exposure time.
    Delay is achieved by slowly raising from reservoir Z height to Z+10
    """
    if uv_enabled:
      # Now turn on the UV LED, and do a move that will take 20 seconds while the UV gels a bit
      output_stream.write(f"M8 ; UV On, slow move\n");
      output_stream.write(f"G1 Z{(RESERVOIR_Z+10):.3f} F{exposure_factor:.3f}\n");
      # OK, LED can go off now
      output_stream.write(f"M9 ; UV Off\n");


def parse_gcode_line(line,scaling):
    """
    Parses a line of GCODE into a dictionary of commands and their values.
    Preserves any trailing comments.
    scaling - multiplies all input command values by this factor
    """
    parts = line.split(';', 1)  # Split into GCODE and comment
    gcode_part = parts[0].strip()
    comment_part = parts[1].strip() if len(parts) > 1 else ""

    if not gcode_part:  # Line contains only a comment
        return None, {}, comment_part

    tokens = gcode_part.split()
    command = tokens[0]
    params = {token[0]: float(token[1:])*SCALE_FACTOR for token in tokens[1:]}
    return command, params, comment_part

def reconstruct_gcode(command, params, comment_part):
    """
    Takes the parsed output from parse_gcode_line and turns it back
    into a GCODE string again.
    But it keeps the scaling and throws away any attempt to move A axis (extruder)
    """
    modified_parts = []

    for k, v in params.items():
        if k == "A":
            continue  # skip A-axis entirely

        if k == "F":
            v = min(FAST_Z, v)  # Clampspeed to max Z speed

        modified_parts.append(f"{k}{v:.5f}")

    param_str = " ".join(modified_parts)
    line = f"{command} {param_str}".strip()

    if comment_part:
        line += f" ;{comment_part}"

    return line

def distance_xy(point1, point2):
    """
    Calculates the Euclidean distance between two points in the XY plane.
    """
    return math.sqrt((point1[0] - point2[0]) ** 2 + (point1[1] - point2[1]) ** 2)

def segment_path (start, end, segment_length):
    """
    Breaks a line segment into smaller segments of specified length, considering only XY distance.
    """
    segments = []
    total_distance = distance_xy(start, end)
    if total_distance <= segment_length:
        return [end]

    num_segments = math.ceil(total_distance / segment_length)
    dx = (end[0] - start[0]) / num_segments  # Increment in X
    dy = (end[1] - start[1]) / num_segments  # Increment in Y

    for i in range(1, num_segments + 1):
        segment_point = [
            start[0] + i * dx,
            start[1] + i * dy,
            start[2]  # Maintain the original Z height from the input
        ]
        segments.append(segment_point)

    return segments

def process_gcode(input_stream, output_stream):
    """
    Processes GCODE lines and breaks toolpaths into segments that can be drawn with a dip pen
    """
    current_safe_z = SAFE_Z
    current_position = [0.0, 0.0, current_safe_z]
    current_layer = 0    # The max height at which we consider we're in the current layer.
    last_probe_position = None
    point_count = PROBE_POINT_LIMIT  # Ensure the probe gets dipped before first point is plotted.
    printed_something = False        # We don't expose the layer before we've printed something

    for line in input_stream:
        line = line.strip()
        # Just pass blank lines through
        if not line:
          output_stream.write(line + '\n')
          continue

        # Strip out all "M" codes
        if line.startswith('M') == True:
          continue

        # Skip any attempts to move the A axis
        if line.startswith('G1 A') == True:
          continue

        # Parse the next GCODE line (Scaling of 1 for now)A
        command, params, comment = parse_gcode_line(line,1.0)

        # Line contains only a comment. If it indicates layer change, expose layer and change safe Z
        if command is None:
          output_stream.write(f"; {comment}\n")
          if comment.startswith("Z:"):
            possible_new_layer_ht = None
            try:
              possible_new_layer_ht = float(comment[2:])*SCALE_FACTOR
            except ValueError:
              pass
            # If we detected a Z value (a) expose the previous layer, and (b) adjust safe Z height.
            if possible_new_layer_ht is not None:
              current_safe_z = possible_new_layer_ht + SAFE_Z
              current_layer = possible_new_layer_ht
              # Now move the probe into the reservoir to protect it from UV
              probe_into_reservoir(current_position,output_stream)
              if printed_something:
                # If we have printed something, expose it.
                # Note: on first layer start there is no output yet!
                expose_to_uv(output_stream,UV_EXPOSURE_LONG);
              # May as well dip the probe while we're here...
              # We're dipping. Reset the dip count
              point_count = 0
              # Return from the dip
              probe_out_of_reservoir_and_return(current_position,output_stream)
          elif comment.startswith("*END"):
            # This is the end of the print. We need to move to the reservoir location and do a Xlong UV exposure
            probe_into_reservoir(current_position,output_stream)
            expose_to_uv(output_stream,UV_EXPOSURE_LONG*2);
            # Take the probe out of the reservoir in case some idiot moves it.
            output_stream.write(f"G1 Z{DIP_SAFE_Z:.3f} F{FAST_Z:.3f} ; Moving to dip-safe Z\n")
            # Nothing else *should* happen after this except turning the motors off.
            # If it does it's out of spec.
            # End of comment handler
          continue

        if command == "G1":
            # Ah, a G1 movement. We're interested in those. Where are we going?
            new_position = [
                params.get("X", current_position[0]),
                params.get("Y", current_position[1]),
                params.get("Z", current_position[2])
            ]

            # Only modify the command if we're close to the work surface.
            if new_position[2] <= current_layer:
                segments = segment_path(current_position, new_position, SEGMENT_LENGTH)

                # Flag indicating we are definitely at safe height, to raise probe for first move.
                segment_move_flag = 0
                for segment in segments:
                    # Check if this point is sufficiently far from the last probe point
                    if last_probe_position is None or distance_xy(last_probe_position, new_position) >= SEGMENT_LENGTH / 2:
                      # We have not probed near this point before. Output it.
                      # Move to safe Z height if not there already
                      if segment_move_flag == 0:
                        output_stream.write(f"G1 Z{current_safe_z:.3f} F{FAST_Z:.3f} ; Moving to safe Z\n")

                      # We're probing a new point. Do we need to check probe dipping?
                      if PROBE_POINT_LIMIT > 0:
                        # See if we've worn all the ink off and need to dip
                        point_count += 1
                        if point_count >= PROBE_POINT_LIMIT:
                            dip_probe(segment,output_stream)
                            # Reset the point count and move a SAFE_Z
                            point_count = 0
                            output_stream.write(f"G1 Z{current_safe_z:.3f} F{FAST_Z:.3f}\n")


                      # Move to segment point
                      output_stream.write(f"G0 X{segment[0]:.3f} Y{segment[1]:.3f} F{FAST_Z:.3f} ; Moving to segment point\n")
                      # Touch down to skimming height if still at SAFE_Z
                      if segment_move_flag == 0:
                        output_stream.write(f"G1 Z{(segment[2]+SKIM_HEIGHT):.3f} F{FAST_Z:.3f} ; Move to skim\n")
                      output_stream.write(f"G1 Z{segment[2]:.3f} F900 ; Touching down gently\n")
                      output_stream.write(f"G1 Z{segment[2]+SKIM_HEIGHT:.3f} F{FAST_Z:.3f} ; Raise probe slightly\n")
                      segment_move_flag = 1 # No longer need to move to SAFE_Z before printing anything
                      printed_something = True
                      # Set the last probed position so we don't touch near it again.
                      last_probe_position = segment
                # We have printed a segment of some kind.
                # If we've printed a dot, return to a safe Z height and note new line start position
                if segment_move_flag != 0:
                  output_stream.write(f"G1 Z{current_safe_z:.3f} F{FAST_Z:.3f} ; Returning to safe Z.\n")
                current_position = new_position
            else:
                # We're above Safe Z, so just execute the existing GCODE with any scaling
                current_position = new_position
                output_stream.write(reconstruct_gcode(command, params, comment) + '\n')
        else:
            # This is not a G1 code, so just pass it through.
            output_stream.write(line + '\n')


def main():
    """
    Main function to handle input and process GCODE.
    """
    usage = (
        "Usage: dipify_gcode.py [input_file] [output_file]\n"
        "\n"
        "If no input_file is provided, reads from standard input.\n"
        "If no output_file is provided, writes to standard output.\n"
    )

    if len(sys.argv) > 1 and ("-h" in sys.argv or "--help" in sys.argv):
        print(usage)
        sys.exit(0)

    infile = sys.stdin  # Default to standard input and output
    outfile = sys.stdout
    input_file = None
    output_file = None

    # Ugly argument parser to get first input GCODE filename, then the output one.
    if len(sys.argv) > 1:
        input_file = sys.argv[1]
    if len(sys.argv) > 2:
        output_file = sys.argv[2]

    # Try to open the IO.
    if input_file:
        infile = open(input_file, 'r')

    if output_file:
        outfile = open(output_file, 'w')

    outfile.write('; File processed by dipify_gcode.py\n')
    process_gcode(infile, outfile)

    # If not using standard input, close the files
    if input_file:
      infile.close()
    if output_file:
      outfile.close()

if __name__ == "__main__":
    main()

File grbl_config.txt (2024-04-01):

$0=10
$1=255
$2=0
$3=7
$4=0
$5=0
$6=0
$10=1
$11=0.010
$12=0.002
$13=0
$20=0
$21=1
$22=1
$23=7
$24=3.000
$25=5.000
$26=250
$27=0.500
$30=1000
$31=0
$32=0
$100=38125.000
$101=38125.000
$102=38125.000
$110=4.000
$111=4.000
$112=4.000
$120=0.100
$121=0.100
$122=0.100
$130=12.000
$131=12.000
$132=10.000

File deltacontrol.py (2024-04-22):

# deltacontrol.py - Prototyping control panel for driving a micro delta stage that uses GRBL
# Released under GPL3 or later by vik@diamondage.co.nz 2024
# Uses the free Zelle portable graphics library, which requires TkInter
import time
import math
import numpy as np
import os
import dcserial
from graphics import *
# This bit contains the stage configuration if you need to fiddle with that
import dcstage

# Nasty Global variables
# ======================
# Units by which manual controls on the panel move.
step_size = 0.1
# Actual start positions of the delta towers. Set im main loop.
# In theory zero, but in practice may be small roundings or plain wrong
tower_zero_offset=(0,0,0)
# Initial axis positions
# These are the numbers the user sees:
x_position, y_position, z_position = 0, 0, 0
# These are the "machine offsets" which hold position when the user redefines an axis to zero.
x_mc_offset, y_mc_offset, z_mc_offset = 0, 0, 0

# Open the default port. Put there so it's all in one place.
def open_port():
    return dcserial.initialize_with_retry(115200,'/dev/ttyACM1')

# Move the TCP to these coordinates using GRBL to move the stage towers
def grbl_move_to(location):
  x, y, z = location
  # Format GRBL G0 command
  GRBL_command = f"G0 X{x:.5f} Y{y:.5f} Z{z:.5f}\n"
  dcserial.send_GRBL_command_ok(ser,GRBL_command)
  
# Move the TCP to (x,y,z) by calculating the new tower positions, and then calling the
# grbl_move_to function to set them.
# Note: [xyz]_mc_offset contains the offsets applied from initial zero when user
# sets an axis position as zero such as when levelling.
def tcp_move_to(pos):
  # Combine the user coordinates with machine coordinates
  # Note: Y is inverted in this hardware, so we flip it.
  offset_xyz=(x_mc_offset+pos[0],y_mc_offset-pos[1],z_mc_offset+pos[2])
  tower_new_position=dcstage.calculate_joint_positions(offset_xyz)
  # Subtract the zero offset from each axis. This should not do anything.
  # However, I have misconfigured things before and it has saved my bacon.
  shifted_tower_position=(tower_new_position[0]-tower_zero_offset[0], tower_new_position[1]-tower_zero_offset[1], tower_new_position[2]-tower_zero_offset[2])
  # Now we move the GRBL axes to put the TCP in the right place
  grbl_move_to(shifted_tower_position)


def draw_axis_location(win, x, y, z):
    # Clear previous axis location text
    if hasattr(win, 'axis_text'):
        win.axis_text.undraw()
    # Draw current axis location text
    axis_location_text = f"Step: {step_size:.4f}    X: {x:.4f}, Y: {y:.4f}, Z: {z:.4f}"
    win.axis_text = Text(Point(win.getWidth() - 180, 20),axis_location_text)
    win.axis_text.draw(win)

# Figures out if the point supplied is inside a specific button
def is_clicked(point, button):
    return button.getP1().getX() < point.getX() < button.getP2().getX() and \
           button.getP1().getY() < point.getY() < button.getP2().getY()


# Replace the variables x, y, and z in a G-code line with provided values.
# Args:
# gcode_line (str): The G-code line containing variables x, y, and z.
# x (float): Value to replace x variable.
# y (float): Value to replace y variable.
# z (float): Value to replace z variable.
# Returns:
# tuple: Tuple containing the modified x, y, and z values.
def replace_xyz_from_gcode(gcode_line, x, y, z):
    # Regular expression pattern to match x, y, and z values
    pattern = r'([XYZ])([-+]?\d*\.?\d+)'
    
    # Find all matches of x, y, and z values in the G-code line
    matches = re.findall(pattern, gcode_line)
    
    # Replace x, y, and z values with provided arguments
    for variable, value in matches:
        value = float(value)
        if variable == 'X':
            x = value
        elif variable == 'Y':
            y = value
        elif variable == 'Z':
            z = value
    
    return x, y, z



# Opens a file dialog for selecting a file from the specified directory.
#
# Args:
# directory (str): The directory to open the file dialog in. Default is the current directory.
#
# Returns:
# str: The path to the selected file, or None if no file is selected.
def get_gcode_file(directory="."):
    # Use tkinter file dialog
    try:
        import tkinter as tk
        from tkinter import filedialog
    except ImportError:
        raise ImportError("Tkinter is required for file dialogs.")

    root = tk.Tk()
    root.withdraw()  # Hide the main window

    # Open file dialog
    file_path = filedialog.askopenfilename(initialdir=directory, title="Select .gcode file", filetypes=[("G-code files", "*.gcode")])

    return file_path

#    # Example usage
#    selected_file = select_gcode_file()
#    if selected_file:
#        print("Selected file:", selected_file)
#    else:
#        print("No file selected.")

#  Reads a specified file line by line and prints lines starting with 'G0', 'G1', or 'G2'.
#
#  Args:
#  file_path (str): The path to the file to be read.
#
#  Returns:
#  None
def print_gcode_lines(file_path):
    try:
        with open(file_path, 'r') as file:
            for line in file:
                # Strip leading and trailing whitespace
                line = line.strip()
                # Check if the line starts with 'G0', 'G1', or 'G2'
                if line.startswith(('G0', 'G1', 'G2')):
                    print(line)
    except FileNotFoundError:
        print("File not found:", file_path)

# Example usage
#file_path = "example.gcode"  # Specify the path to your file
#print("G-code lines:")
#print_gcode_lines(file_path)
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

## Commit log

2024-04-01 GRBL settings
    These are the settings used to drive the OpenFlexure delta stage with 0.9 degree/step NEMA17 motors.
    [grbl_config.txt]
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2024-04-03 Update deltacontrol.py to use modules properly
    Also I'd missed a serial command that wasn't modular.
    [deltacontrol.py]
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2025-01-07 Printable box to hold delicate probes
    SVG file is for cutting fancy acrylic top and bottom panels so you can see inside.
    [probebox.scad]
2025-01-07 Update maus_stage.scad -version, todo etc.
    Added version string V0.01
    Added TODO
    Put version text on axis and table
    Removed excess 10U strips from build plate
    Enlarged light well
    [maus_stage.scad]
2025-01-29 Update metriccano.scad - hole size changed. Square & elongated plates.
    Made screw holes slightly smaller as they were always loose.
    Renamed screw hole to avoid name collisions.
    Added a round/square unit to make square-ended beams easier to write.
    metriccano_plate can now have square corners.
    Added metriccano_elongated_plate, with elongated holes down one edge.
    Added metriccano_triangular_plate as a simple 3-holed equilateral triangle.
2025-01-31 Update metriccano.scad - adjustment bracket
    Added a bracket for joining poorly aligned parts.
    Also fixed the tab module so it can be made with a single row of holes without using depricated for loops.
2025-02-03 Update metriccano.scad - angle strip & tidying
    Updated description of triangle plate.
    Put default length value for slot strip.
    Gave the base of the adjustment strip a variable length.
    Added a strip with an angle bent into it.
2025-02-03 Create maus_complementary.scad
    A complementary flexure stage designed to be more compact and portable than the XY Table in maus.scad
    Attaches to a sheet of 10mm pitch pegboard or a lasercut base plate.
    Initially designed to be compact enough to fit under a binocular microscope, but turns out to be pretty good all round.
    [maus_complementary.scad]
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2025-02-16 Create prusaslicer_filter.sh
    A simple script to take the PrusaSlicer-generated GCODE filename, pass it to a python filter, and replace the Prusa file with the modified one. Some debug deliberately left in.
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2025-04-17 Update m3_parts.scad - M3 hole boolean fix
    Minor shift to avoid ugly booleans
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2025-04-25 Rename maus_stage.scad to maus_stage_deprecated.scad
    Uses original XY Flexure Table, now replaced with the complementary flexure table.
    [maus_stage_deprecated.scad]
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2025-04-25 Update flexure_linear_coupling.scad
    Moved all parts into a module so the coupling can be used as an include file
    [flexure_linear_coupling.scad]
2025-04-25 Update maus_complementary.scad - extensive
    Include flexure coupling.
    Now Version 0.03
    Moved a lot of variables and NEMA17 plate to the top of the file.
    Added UV LED to stage.
    Removed old stage design.
    Changed magnet to thicker 30mm one.
    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
    [maus_complementary.scad]
2025-04-26 Update maus_complementary.scad
    Somehow ended up with Maus Stage in there. Replaced content.
    [maus_complementary.scad]
2025-04-26 Update maus_axis_driver.scad
    Wrong header, replaced.
    Nuts in bearing pillars now standard M3 captive slots.
    [maus_axis_driver.scad]
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2025-05-01 Update flexure_linear_coupling.scad
    Made the entrance to the nut hole a smidgin wider.
    [flexure_linear_coupling.scad]
2025-05-01 Create maus_probe.scad
    Initial entry of Z axis probe parts in separate file.
    [maus_probe.scad]
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2025-05-01 Update maus_complementary.scad - more thumbwheels
    Each microscope holder may need 5 thumbwheels
    Also made plate selection a true/false switch
    [maus_complementary.scad]
2025-05-02 Update maus_complementary.scad
    Idiot put the 'Y' axis tag label on the wrong side. Doh!
    [maus_complementary.scad]
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2025-05-05 Update maus_complementary.scad Nut & bracket sortout for documentation release.
    Added many captive nuts as assembly was a swine without them.
    Pole stand now has a slightly larger hole.
    Fewer adjustment brackets and misc Metriccano strips now the Z Tower has been done.
    Reposition parts on the build plates to suit above.
    One large and one small microscope clamp.
    [maus_complementary.scad]
2025-05-05 Update maus_probe.scad - shorter probe arm
    Changes to Z tower meant probes were too long.
    [maus_probe.scad]
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2025-05-07 Current MAUSC V0.03 GRBL config for RAMPS boards
    Your steps/mm may vary. Note that config is based on 1mm = 1 micron as GRBL does not do well with small numbers.
    [grbl_config_RAMPS_20250507.txt]
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2025-05-20 Update grbl_config_RAMPS_20250507.txt
    Updated erroneous step pin inversion and inverted axis.
    [grbl_config_RAMPS_20250507.txt]
2025-05-25 Update maus_axis_driver.scad
    Removed flexure coupling as it needs to be printed separately.
    [maus_axis_driver.scad]
2025-05-25 Update flexure_linear_coupling.scad
    Widened nut coupling hole to hold more nut.
    Made flexures thinner and more flexible.
    Increased resolution of shell.
    Turned into stand-alone SCAD file as it needs to be printed with brim.
    [flexure_linear_coupling.scad]
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2025-05-25 Baseboard mounts
    Metriccano parts to stack two baseboards, giving room between them for driver electronics
    [maus_baseboard_mounts.scad]
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2025-08-12 Update maus_complementary.scad to initial 0.04
    Reduced flexure clearance from 3mm to 2mm.
    Outer flexure pairs and inner flexure pairs now have both flexures the same length.
    Table flexure attachment points now wrap around the mounts on the Outer Frame.
    Outer Frame sides now have captive nut holes.
    Made printable plates selectable by numbers rather than a boolean.
    [maus_complementary.scad]
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2025-08-24 Update metriccano.scad Screw cavity and flat end strips
    The Metriccano screw cavity has an option of being inverted, which adds a temporary support to the centre of the screw hole.
    A metriccano_strip_flatend() of the Metriccano strip always has one flat end. Useful for adding tabs to parts etc.
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2025-08-29 Update maus_complementary.scad - Major X & Y Flexure changes
    Added captive nut cavities to frame sides
    Y Drive Flexure now connexts directly to Flexure Table
    X Flexure now complementary to allow Y movement
    [maus_complementary.scad]
2025-08-29 Update maus_axis_driver.scad - more movement, extra mounting holes
    Lowering the wall on the Axis Motor Pillar Assembly to allow larger range of movement
    Added mounting holes for extra rigidity
    Through holes on NEMA plate to allow pillar screw overtravel
    [maus_axis_driver.scad]
2025-08-29 Update maus_z_tower.scad - move reinforcement for X collision
    Moved one beam and added reinforcement to avoid collisions with new X flexure.
    [maus_z_tower.scad]
2025-08-30 Update maus_z_tower.scad - taller tower
    Tower now one unit taller. Boosters no longer needed for tall NEMA17 motors.
    [maus_z_tower.scad]
2025-08-30 Update maus_complementary.scad - removed 3u boosters
    Boosters no longer needed as the Z Tower is slightly taller.
    [maus_complementary.scad]
2025-09-13 Update maus_parallelogram_axis_driver.scad - cranked arms
    Pivot arms now cranked, attachment points outside the frame. Still too long overall.
    [maus_parallelogram_axis_driver.scad]
2025-09-17 Update flexure_linear_coupling.scad - thicker joints
    The joints between curved flexures sometimes came out only one filament thick when sliced, so I made them a teensy bit thicker.
    [flexure_linear_coupling.scad]
2025-09-17 Update maus_parallelogram_axis_driver.scad - Cranked arms
    The arms are now cranked, allowing the mounts to be placed on the outside of the flexure. They are now also capable of being at an angle of other than 45 degrees, which allows long arms in a shorter frame. Added parts for anti-backlash.
    [maus_parallelogram_axis_driver.scad]
2025-09-20 Update metriccano.scad - tighter nut slots, strips can be square-ended
2025-09-20 Update maus_parallelogram_axis_driver.scad -new anchors and limit switch parts
    The anchor now has a limit switch tab on it, and the nuts are on the other side of the live end. Some rudimentary parts added to hold a limit switch.
    [maus_parallelogram_axis_driver.scad]
2025-09-28 Update metriccano.scad - Inverted nut, slotted part changes
    Captive nuts can now be inverted, and print with built-in support for central hole.
    A new slot strip with at least one flattened end, and an extended blank section, for making tabs.
    Ordinary slotted strips can now be a fractional number of holes in length.
2025-09-28 Update maus_parallelogram_axis_driver.scad - Cranked arms, new siwtch and support structure.
    Arms cranked to avoid hitting the Nut Bar bearing. Lower Nut Bar added to reduce Drive Screw Wobble.
    Adjustable limit switch bar added.
    Rudimentary case compatible with V0.04 architecture added.
    New brackets to attach Axis Driver to XY Table flexures.
    [maus_parallelogram_axis_driver.scad]
2025-10-06 Update maus_complementary.scad - Z Flexures
    Added complementary flexures to constrain vertical movement on the Z Axis.
    [maus_complementary.scad]
2025-10-06 Update maus_z_tower.scad - to fit linear axis driver
    Moved supports around a lot to fit the V0.05 linear "parallelogram" driver.
    [maus_z_tower.scad]
2025-10-06 Update maus_parallelogram_axis_driver.scad - moving from initial prototyping
    Many changes. Notably drive screw now has bearings at both ends, the limit switch is on the rear of the frame, and the number of mounting holes has been rationalised.
    [maus_parallelogram_axis_driver.scad]
2025-10-06 Update maus_probe.scad - 3 DoF probe mount & length
    Probe mounting system completely changed for V0.05 to have 3 DoF, and the Probe Tip Arm made shorter due to longer length of a parallelogram Axis Driver.
    [maus_probe.scad]
2025-10-06 Update metriccano.scad - smaller holes, inverted nut cavity, extended tabs
    The holes have been reduced in diameter to reduce loose tolerances.
    Nut cavities can now be inverted and have built-in support to stop the centre collapsing.
    Tabs can be extended at the attachment end, and a bug whereby single hole tabs didn't show the hole has been fixed.
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2025-10-10 Update probebox.scad - Added keeper as V0.05 probes cannot be screwed to box
    [probebox.scad]
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2025-11-08 Update dipify_gcode.py - stop probe scraping along at skim height
    Slowed FAST_Z down a bit due to vibration - could probably be increased again.
    Fixed move to dip in case object gets taller than dip height.
    Modifiy all speed commands so they do not exceed FAST_Z.
    Ignore all movement on A axis.
    Set height after returning from dip to current_safe_z rather than arbitrary +10um
    [dipify_gcode.py]
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2025-11-21 Update maus_parallelogram_axis_driver.scad - improved anti-backlash tension components
    Renamed nut_bar as there are now two of them.
    Enlarged hooks for anti-backlash bands.
    Marked experimental NEMA holder as experimental.
    Added booster to give more tension to bands if needed.
    Removed unused code.
    Rearranged printable parts plate.
    [maus_parallelogram_axis_driver.scad]
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2026-02-14 Update maus_z_tower.scad - Minor tweak to prevent mesh holes in OpenSCAD
    [maus_z_tower.scad]
2026-02-18 Update maus_pika.scad - Added base, added Stage flexure clearance
    [maus_pika.scad]
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2026-02-19 Update maus_pika.scad - fixing flexure rotation & Z tower height
    [maus_pika.scad]
2026-02-20 Update maus_pika.scad - Joined top Y flexures, shortened Z Tower 10mm, moved microscope bracket right 5mm
    [maus_pika.scad]
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2026-02-20 Update metriccano.scad Made screwdrive access holes, flatend strip can now be nutted, fixed overlapping nut holes in l_plate
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2026-02-23 Update maus_pika.scad - Fixedd bottomless Driver nut slot, moved microscope mount closer to centre.
    [maus_pika.scad]
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2026-02-28 Update maus_pika.scad Frame stiffened. Z Tower back from centre by 10mm
    [maus_pika.scad]
2026-03-08 Update maus_pika.scad - Reinforced frame, Z Tower takes a step back, added microscope pole clips, Stage nuts accessible by mere mortals.
    [maus_pika.scad]
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2026-03-09 Update maus_pika.scad - Moved Z Tower back, put all loose bits on one print plate
    [maus_pika.scad]
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2026-03-09 Update maus_pika.scad - Integrated feet and base, corrected Stage bracket height, improved visualisation.
    First with a V0.01 label.
    [maus_pika.scad]
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2026-03-09 Update maus_pika.scad - metriccano fix
    [maus_pika.scad]
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2026-03-19 Creates GCODE for X & Y axis vernier patterns to determine backlash
    [backlash_vernier.py]
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2026-03-23 Update levelling_probe.py Now 2mm square probed, corrected safe height report.
    [levelling_probe.py]
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2026-04-19 Update pika_probe.scad - header correction
    [pika_probe.scad]
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2026-05-14 Update m3_parts.scad - Added support material for inverted nut cavities, put conical side on thumbscrews.
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2026-06-07 Update pika_xy.scad - Stage mount holes were in the wrong place.
    [pika_xy.scad]
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2026-06-28 Fix syntax errors in pika_axis_driver.scad
    [pika_axis_driver.scad]

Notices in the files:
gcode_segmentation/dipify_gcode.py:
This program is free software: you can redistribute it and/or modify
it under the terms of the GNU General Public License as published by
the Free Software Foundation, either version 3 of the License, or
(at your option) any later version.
